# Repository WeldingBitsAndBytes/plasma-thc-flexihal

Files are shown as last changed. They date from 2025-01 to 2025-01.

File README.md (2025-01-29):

# WIP

A THC control board that can connect to a Expatria Flexihal for controlling a plasma cutter

I've highlighted BOMs for each major component, but I've left some things like hookup wires,
pins, etc to your own design and in particular your own plasma cutter.

## THC Divider Board

`thc_divider_board` directory contains a Kicad PCB designed to isolate the raw plasma cutter 
measurements from the MCU. The PCBs were designed with Oshpark in mind, in particular the
"After Dark" style just for fun. As such, there is minimal silkscreening.

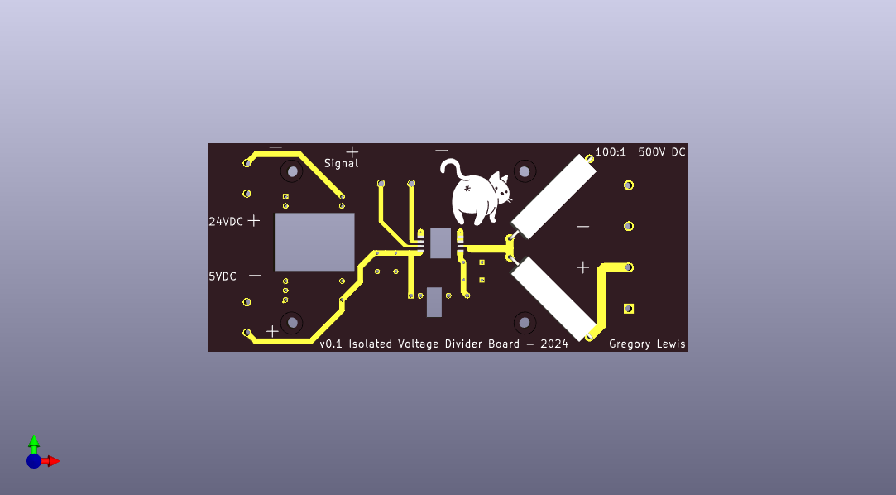
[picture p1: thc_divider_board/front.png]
front


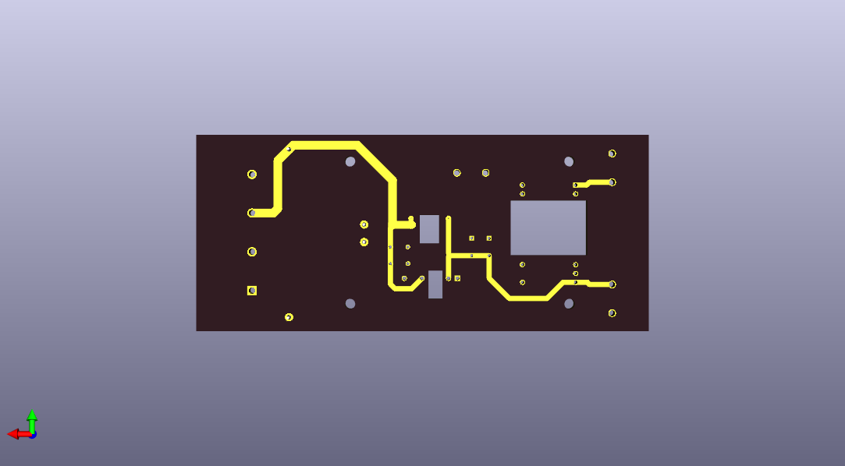
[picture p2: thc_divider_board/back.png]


The board is intended to be powered by an internal 24VDC power supply within the plasma cutter. The 
plasma cutter's power supply is protected by a 6KVDC reinforced DC-DC converter. The low-side of the 
isolation amplifier is powered by another isolation DC-DC converter fed from the main DC-DC 
converter. This secondary 5V DC-DC converter also provides power for the MCU.

The MCU is intended to be something like an Arduino Nano. Almost any other MCU would work but these
are cheap, small, and just fine for this application.

## Nano Voltage Sender

`nano_voltage_sender` contains the sketch for the Arduino Nano. It uses an external Vref voltage source
to normalize out the voltage for more accurate readings. It uses the 2V reference source to match the
0-2V output from the THC divider board.

The signal is connected to the ADC. The MCU is connected to a https://www.dfrobot.com/product-2588.html 
UART Fibre Optic Transceiver

BOM:

| Part | Quantity | Notes |
| --- | --- | ----- |
| Arduino Nano | 1 | Or similar |
| UART Fiber Optic Transceiver | 1 | https://www.dfrobot.com/product-2588.html |
| LM4040 Voltage Reference | 1 | Or similar - eg: https://www.adafruit.com/product/2200 |
| Arduino Nano Screw Terminal Adapter | 1 | https://store-usa.arduino.cc/products/nano-screw-terminal is really nice |
| SC Fibre Optic Cable | 1 | Recommend duplex so you can fire a relay for plasma control |

## Teensy Quadrature Encoder

The `teensy_quadrature_encoder` directory contains the sketch for a Teensy 4 to convert from
serial to quadrature encoding. The Teensy 4 was chosen for its high speed and ability to measure nanoseconds 
for precise timings.  The quadrature encoding is then used to interface with a Expatria FlexiHAL and by 
extension LinuxCNC for torch height control. Similarly, this Teensy will also have a UART Fibre Optic 
Transceiver to talk to the Nano

BOM:

| Part | Quantity | Notes |
| --- | --- | ----- |
| Teensy 4 | 1 | Or similar |
| UART Fiber Optic Transceiver | 1 | https://www.dfrobot.com/product-2588.html |
| Screw terminals | 8 | Have enough screw terminals for the uart serial, and power output, and quadrature encoder output |

## FlexiHAL Hookup and Configuration

BOM:

| Part | Quantity | Notes |
| --- | --- | ----- |
| Ethernet cable, TIA 568B straight-through | 1 | |
| Flexihal! | 1 | Duh |

More to come :)

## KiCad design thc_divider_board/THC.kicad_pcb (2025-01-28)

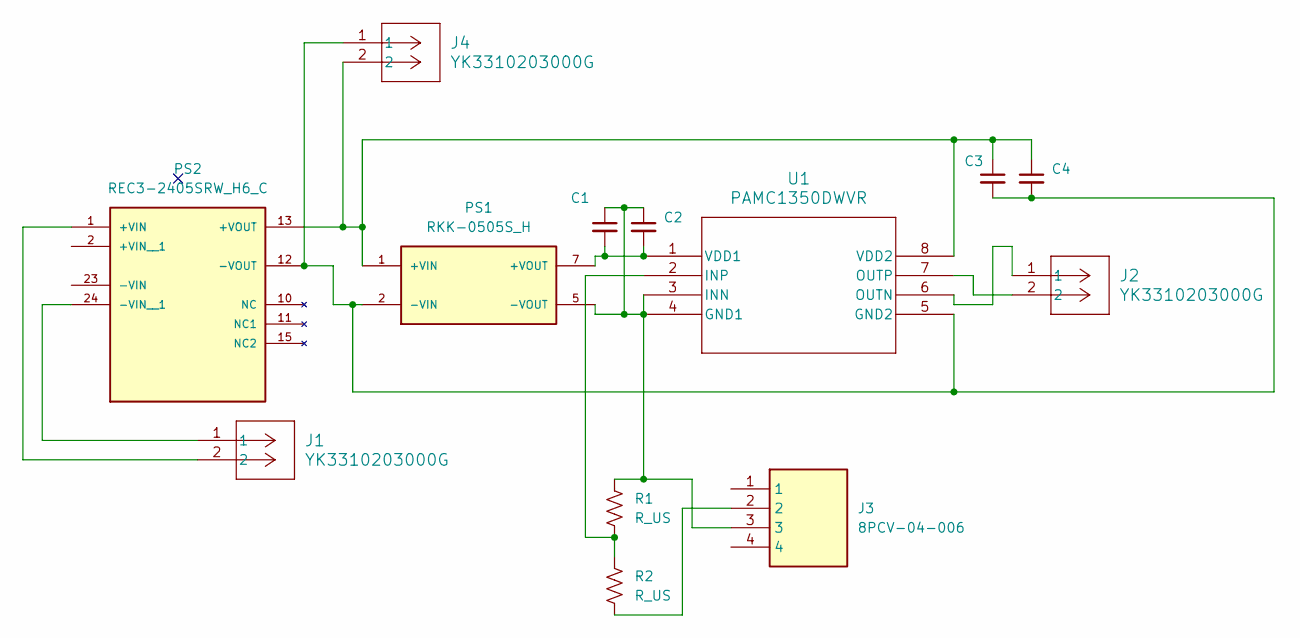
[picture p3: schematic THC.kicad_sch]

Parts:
C1, C2, C3, C4: C_Small; CAP_R7540_TDK
J1, J2, J4: YK3310203000G; CONN_YK331020xx00G_AMP
J3: 8PCV-04-006; SHDR4W114P0X1112_1X4_4628X2032X1956P; Mouser Part Number 571-814376570
PS1: RKK-0505S_H; CONV_RKK-0505S_H; PARTREV 0/2023
PS2: REC3-2405SRW_H6_C; CONV_REC3-2405SRW_H6_C; PARTREV N/A
R1, R2: R_US; R_Axial_Power_L25.0mm_W6.4mm_P30.48mm
U1: PAMC1350DWVR; U_PAMC1350DWVR_TEX

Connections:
unnamed: J3.2, R2.2
unnamed: C3.1, C4.1, J4.2, PS1.1 (+VIN), PS2.13 (+VOUT), U1.8 (VDD2)
unnamed: C1.2, C2.2, PS1.7 (+VOUT), U1.1 (VDD1)
unnamed: C3.2, C4.2, J4.1, PS1.2 (-VIN), PS2.12 (-VOUT), U1.5 (GND2)
unnamed: C1.1, C2.1, J3.3, PS1.5 (-VOUT), R1.1, U1.3 (INN), U1.4 (GND1)
unnamed: J1.2, PS2.1 (+VIN)
unnamed: J1.1, PS2.24 (-VIN__1)
unnamed: R1.2, R2.1, U1.2 (INP)
unnamed: J2.1, U1.6 (OUTN)
unnamed: J2.2, U1.7 (OUTP)

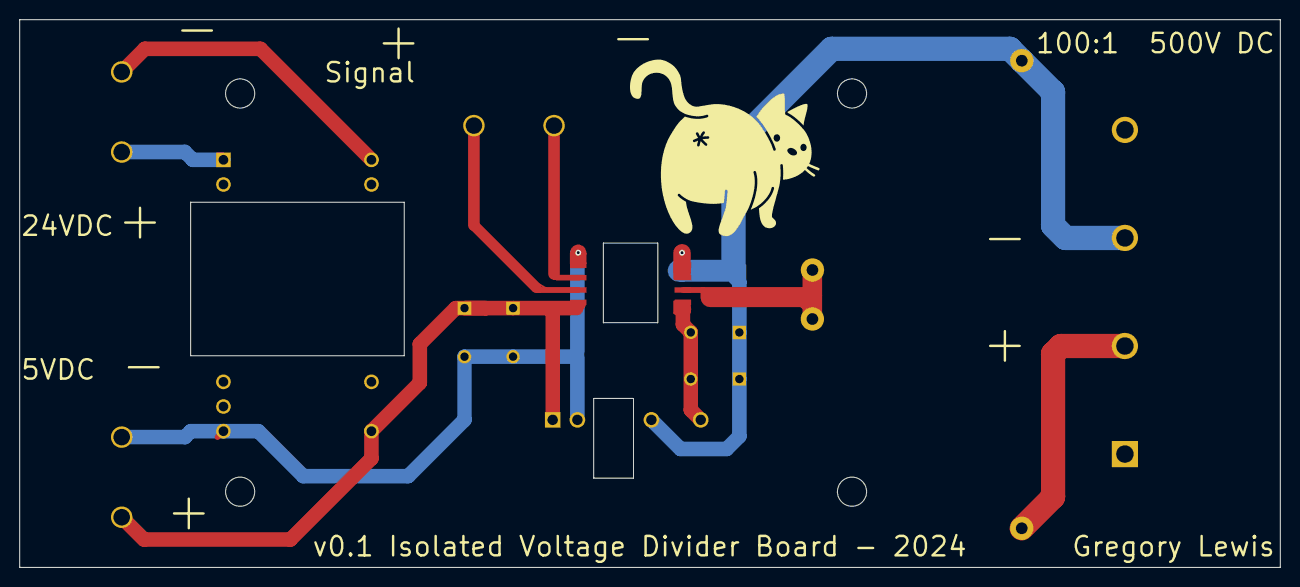
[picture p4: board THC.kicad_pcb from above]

Board: 2 copper layers, 129.8 x 56.4 mm, 13 parts (0 on the bottom side), 10 nets.

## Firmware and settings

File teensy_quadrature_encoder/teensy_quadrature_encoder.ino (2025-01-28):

// Quadrature Generator
// https://wokwi.com/projects/403218793081155585

// Define the output pins



#include "Arduino.h"

namespace cycles64
{
    uint64_t get();

    namespace // private -----------------------------
    {
        uint32_t oldLow = ARM_DWT_CYCCNT;
        uint32_t curHigh = 0;

        void SNVS_isr(void)
        {
            SNVS_HPSR |= 0b11; // reset interrupt flag
            get();             // call to check for overflow
            asm("dsb");        // prevent double calls of the isr
        }

    } // end private namespace <<---------------------

    uint64_t get()
    {
        noInterrupts();
        uint32_t curLow = ARM_DWT_CYCCNT;
        if (curLow < oldLow) // roll over
        {
            curHigh++;
        }
        oldLow = curLow;
        uint64_t curVal = ((uint64_t)curHigh << 32) | curLow;
        interrupts();

        return curVal;
        
    }

    void begin()
    {
        // disable periodic snvs interrupt
        SNVS_HPCR &= ~SNVS_HPCR_PI_EN;
        while ((SNVS_HPCR & SNVS_HPCR_PI_EN)) {}

        // interrupt frequency 1Hz
        SNVS_HPCR = SNVS_HPCR_PI_FREQ(0b1111);

        // enable periodic snvs interrupt
        SNVS_HPCR |= SNVS_HPCR_PI_EN;
        while (!(SNVS_HPCR & SNVS_HPCR_PI_EN)) {}

        attachInterruptVector(IRQ_SNVS_IRQ, SNVS_isr);
        NVIC_SET_PRIORITY(IRQ_SNVS_IRQ, 255); // lowest
        NVIC_ENABLE_IRQ(IRQ_SNVS_IRQ);
    }
}




#define pinApos 3
#define pinAneg 4
#define pinBpos 10
#define pinBneg 11

// Define the state machine states
enum State {STATE0, STATE1, STATE2, STATE3};
State currentState = STATE0;

// Timing variables
uint64_t previousNanos = 0;
float interval = 1000.0; // 1000 nanoeconds for each state


int content;
int old = "";
const byte numBytes = 32;
byte receivedBytes[numBytes];
byte numReceived = 0;
boolean newData = false;


void setup() {
  Serial.begin(8000000);
  //while (!Serial);

  // Initialize the output pins
  pinMode(pinApos, OUTPUT);
  pinMode(pinAneg, OUTPUT);
  pinMode(pinBpos, OUTPUT);
  pinMode(pinBneg, OUTPUT);

  pinMode(13, OUTPUT);

  // Initialize the pins to a known state
  digitalWrite(pinApos, LOW);
  digitalWrite(pinAneg, LOW);
  digitalWrite(pinBpos, LOW);
  digitalWrite(pinBneg, LOW);

  digitalWrite(13, HIGH);

  cycles64::begin();

  Serial3.begin(1000000);
  //while (!Serial3);
}

void loop() {
  recvBytesWithStartEndMarkers();
  parseNewData();
  quadGenerator();
}

void recvBytesWithStartEndMarkers() {
  /*
  profiler_t profiler(
    (String("Time spent in ") + 
    String(__FUNCTION__) + 
    String("()")).c_str());
  */

    static boolean recvInProgress = false;
    static byte ndx = 0;
    byte startMarker = 0x3C;
    byte endMarker = 0x3E;
    byte rb;
   
    while (Serial3.available() > 0 && newData == false) {
        rb = Serial3.read();
        if (recvInProgress == true) {
            if (rb != endMarker) {
                receivedBytes[ndx] = rb;
                ndx++;
                if (ndx >= numBytes) {
                    ndx = numBytes - 1;
                }
            }
            else {
                receivedBytes[ndx] = '\0'; // terminate the string
                recvInProgress = false;
                numReceived = ndx;  // save the number for use when printing
                ndx = 0;
                newData = true;
            }
        }

        else if (rb == startMarker) {
            recvInProgress = true;
        }
    }
}

void parseNewData() {
  /*
  profiler_t profiler(
    (String("Time spent in ") + 
    String(__FUNCTION__) + 
    String("()")).c_str());
  */
  if (newData == true) {
    newData = false;
    int content = (receivedBytes[0]<<8) + receivedBytes[1];
    if (content != old) {
      old = content;
      unsigned int frequency = (content * 50) + 1000; // Range from 1khz to 11.23khz
      interval = (1000000.0 / frequency / 4) * 1000.0; // Convert frequency to interval and divide by 4 as we need to do 4 things in a cycle 
    }
  }
}

void quadGenerator(){
  /*
  profiler_t profiler(
    (String("Time spent in ") + 
    String(__FUNCTION__) + 
    String("()")).c_str());
  */
  // Get the current time in nanoseconds
  // Check if the interval has passed

  if (cycles64::get() - previousNanos >= interval) {

    // Advance the state machine
    switch (currentState) {
      case STATE0:
        digitalWrite(pinApos, HIGH);
        digitalWrite(pinAneg, LOW);
        currentState = STATE1;
        break;

      case STATE1:
        digitalWrite(pinBpos, HIGH);
        digitalWrite(pinBneg, LOW);
        currentState = STATE2;
        break;

      case STATE2:
        digitalWrite(pinApos, LOW);
        digitalWrite(pinAneg, HIGH);
        currentState = STATE3;
        break;

      case STATE3:
        digitalWrite(pinBpos, LOW);  
        digitalWrite(pinBneg, HIGH);
        currentState = STATE0;
        break;       
    }
    
    previousNanos = cycles64::get();

  }
}

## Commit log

2025-01-28 Initial dump of project files (#1)
    [THC.kicad_pcb, THC.kicad_sch]
2025-01-29 Bom (#4)
